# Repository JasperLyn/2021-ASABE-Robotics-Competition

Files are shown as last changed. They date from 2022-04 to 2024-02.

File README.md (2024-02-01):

# Strawberry Nursery Robot - Mr. Y

This is a repository for a project in **2021 ASABE Robotics Competition**, which includes circuit design document, robot control, machine vision and Structure design file. If you are interested in ASABE Robotics Competition, please search more information at official website of [ASABE Robotics Competition](https://asabe.org/Robotics).

## Guide

There are four main parts of the robot.

+ Mechanical Structure (please refer to `Model`)
+ Circuit Design (please refer to `Circuit Design`)
+ Machine Vision (please refer to `src`)
+ Control (please refer to `src`)

## Video Presentation
Team Qizhen Lakers- 2nd Place (Best Electronic Presentation) in the 2021 ASABE Robotics Competition (https://www.youtube.com/watch?v=8VvXFQ61o2o "Team Qizhen Lakers- 2nd Place (Best Electronic Presentation) in the 2021 ASABE Robotics Competition")

## Paper Report

For detailed technical development information, please refer to `Report Document/The Report of Qizhen Lakers`

## Definition of Design Objectives and Criteria

The robot to be designed for this competition should have the ability to recognize the white and yellow leaves of strawberry plants and complete the counting display. In order to achieve the goal perfectly, a detailed and specific division was made to complete the task efficiently and accurately. The sub-points are as follows.

1. Robot needs to have a navigation function without guidelines.
2. Identify white flowers and yellow leaves on each strawberry plant.
3. Transfer detection results of individual plants to a server program for scoring and field map generation.
4. Minimize the weight of the robot and increase the contact area to reduce the pressure.
5. No damage to the plant.
6. No human intervention to the robot.
7. Have a start button that judges can use to initiate a competition trial and an emergency stop button to fully shut down the entire system.

In the design of robot, we are committed to assure better performance, stronger environmental adaptability, and expandability with more development prospects.

## Originality

### Originality

#### Innovative Linkage Design

We use the combination mechanism of slider and linkage to realize the full unfolding of double cameras bracket and create the development condition for double sides detection. And the linkage mechanism has strong scalability, which can reach different unfolding results by adding nodes, connecting rods or linkage structures to meet a variety of needs, and can also add end-effectors at the end of the linkage to achieve more functions.

#### Lower Pressure

We adopt the crawler trolley structure and make the optimal design for the actual production situation of field operation by calculating and selecting the appropriate size of active wheels, tensioning wheels and load-bearing wheels and determining the optimal spacing to share the pressure to the maximum extent and reduce the impact on soil compaction.

#### Infrared-Sensor Tracking

Since we make the robot travel between the board where the strawberry plants were placed and the board as the boundary of the field, we only need to install the infrared sensor at a suitable height (That is, slightly below the thickness of the board on which the strawberry plants are placed), adjust the sensitivity of the signal received by the infrared sensor, and keep the robot moving in a straight line in the desired area by making reasonable use of the differential speed rotation of the stepper motor through the signal measured by the infrared sensor.

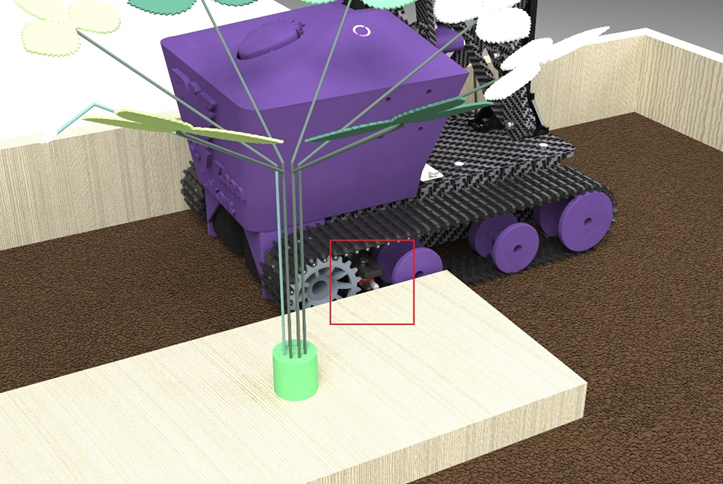
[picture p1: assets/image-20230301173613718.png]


#### Supplemental Light Source

By increasing the fill light band, we make the recognition conditions within the controllable range, eliminate the influence caused by different environmental backgrounds, increase the contrast between the recognition target and the background, and make the robot have better self-adaptability.

#### Multi-threaded Process

We use Raspberry Pi as both processor and control component, and all electronic devices of the robot are controlled through the Raspberry Pi. Calling Python's multi-process module, 3 processes of Raspberry Pi run simultaneously, thus giving higher performance and increasing working speed. The tasks of motor and servo rotation, simultaneous image processing recognition of cameras on both sides and wireless transmission are realized.

#### Remote Emergency Brake

Through the wireless transmission module and Bluetooth module of Raspberry Pi, we designed several remote emergency braking solutions. Although there are already both start switch and emergency brake switch on the robot, considering that there are certain safety hazards of actually approaching the brake when an unpredictable emergency occurs, we made a remote emergency brake switch, which is connected to the Bluetooth module, thus controlling the operation of the Raspberry Pi. In addition, using WIFI wireless communication technology, we can access the graphical interface of the Raspberry Pi for operation. Since all the robot components are controlled by the Raspberry Pi, we can stop the operation of the Raspberry Pi at any moment and thus stop the robot operation. Of course, this does not allow the robot to cut off the power supply system, so we designed an emergency brake switch on the robot to directly cut off the power supply.

## Hardware Description of the Mechanical Structure

### Crawler Structure

In order to reduce the impact on soil compaction and to allow the robot to adapt to a wider range of road environments, we designed a tracked travel mechanism.

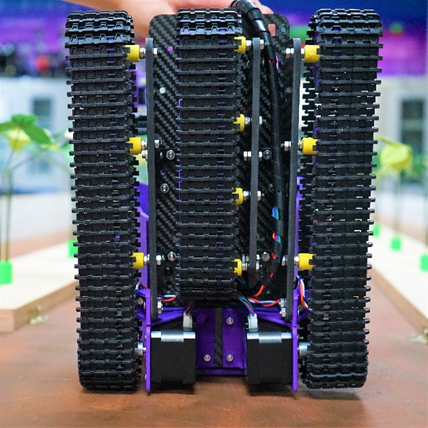
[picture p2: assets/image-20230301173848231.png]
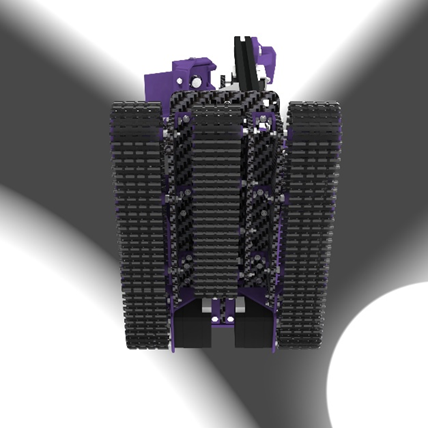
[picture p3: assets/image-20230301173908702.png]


The outer two tracks are long tracks with a ground length of 223.5 mm and a width of 45 mm, equipped with one active wheel, one tensioning wheel and two load-bearing wheels. The middle track is a short track with a ground length of 160 mm and a width of 45 mm, and is equipped with four load-bearing wheels. By reviewing the relevant literature, we calculated the radius and spacing of the active wheel, tensioner wheel and load-bearing wheel. Under the size limitation, we selected the optimal size and spacing.

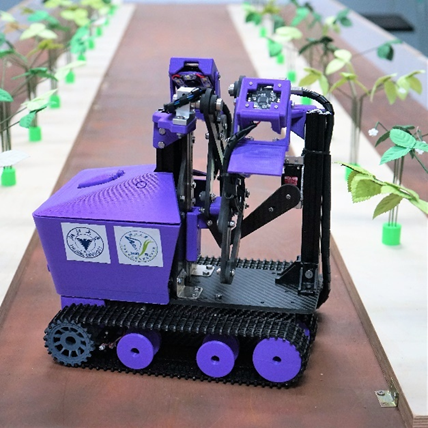
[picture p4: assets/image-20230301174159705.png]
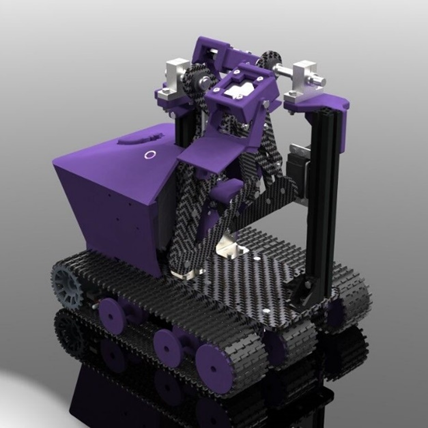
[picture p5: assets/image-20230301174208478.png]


| **Type  of wheel**  | **Radius** |
| :---: | :---: |
| Active  wheel | 25.65  mm  |
|  Tensioning  wheel  | 26.65  mm  |
| Load-bearing  wheel | 20.00  mm  |

### Expanded Mechanical Structure

To simplify the actuator, we use a slide rail and a single-degree-of-freedom extension mechanism with multiple links to extend the camera for detection. The multi-stage linkage is articulated by screws and lock nuts, connected to the slide rail by slider connectors, and uses bearings at some of the connections to reduce frictional resistance, and rotates, lifts, and extends under the drive of the servo. As shown in Figure 5-5 and Figure 5-6, with the rational design of 4 connecting rods on each side (8 in total on both sides), we achieved to expand the robot from the initial size of 300 mm × 209.2 mm × 292.5 mm to 300 mm × 440 mm × 528 mm.

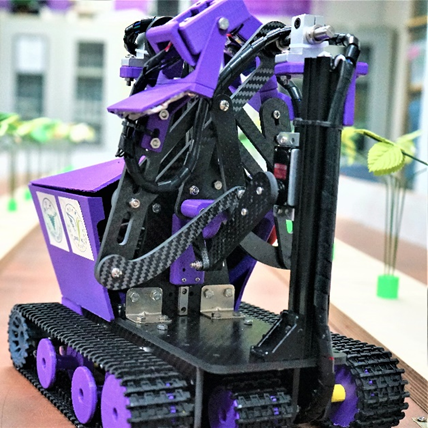
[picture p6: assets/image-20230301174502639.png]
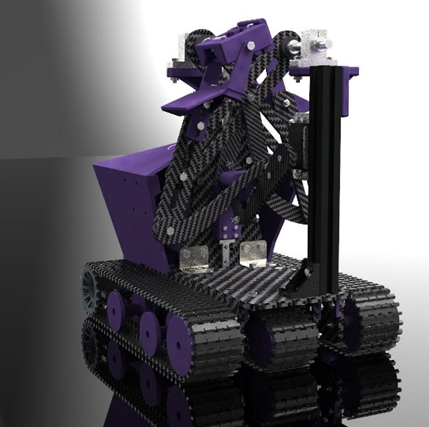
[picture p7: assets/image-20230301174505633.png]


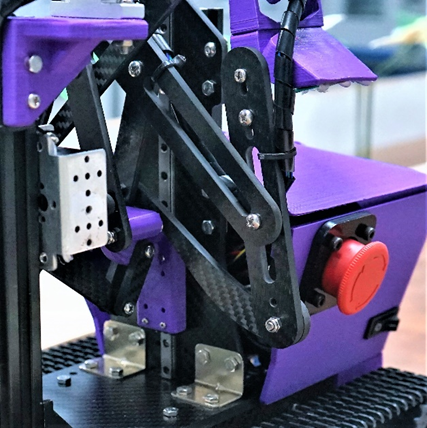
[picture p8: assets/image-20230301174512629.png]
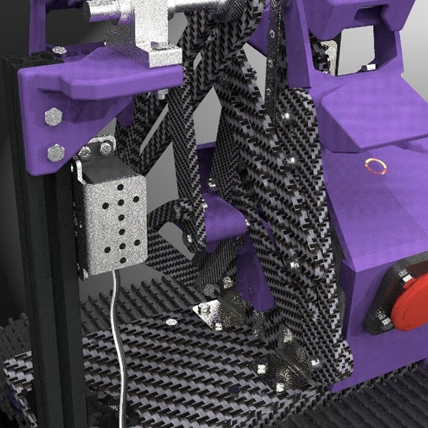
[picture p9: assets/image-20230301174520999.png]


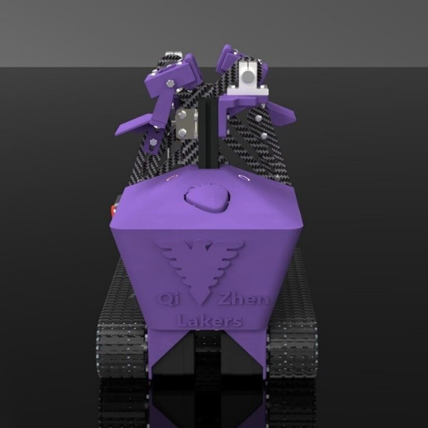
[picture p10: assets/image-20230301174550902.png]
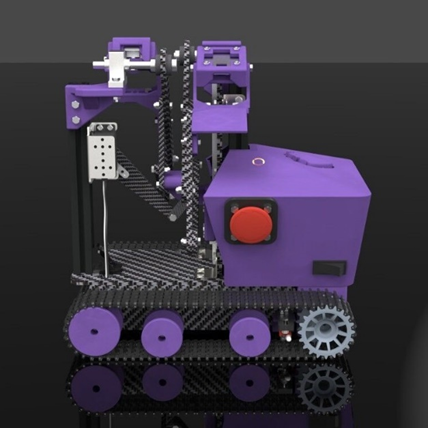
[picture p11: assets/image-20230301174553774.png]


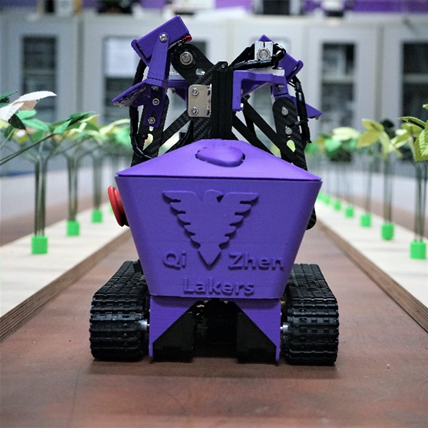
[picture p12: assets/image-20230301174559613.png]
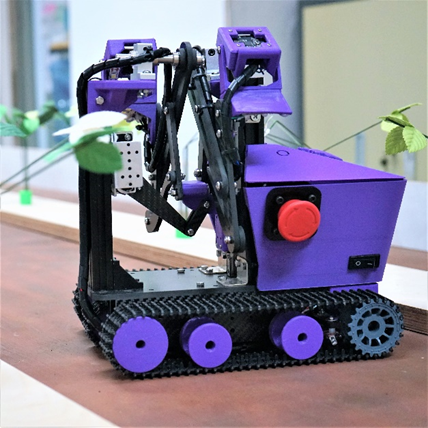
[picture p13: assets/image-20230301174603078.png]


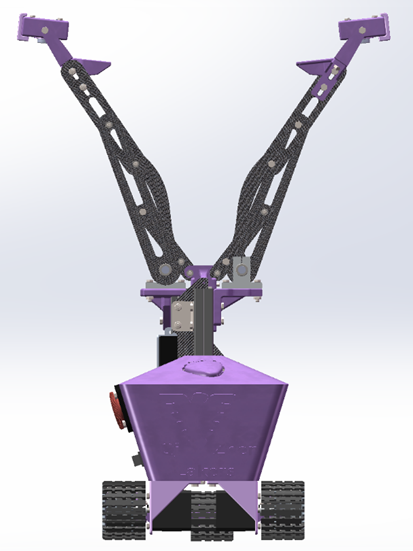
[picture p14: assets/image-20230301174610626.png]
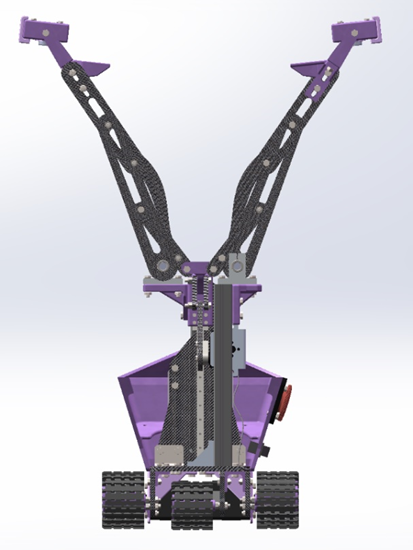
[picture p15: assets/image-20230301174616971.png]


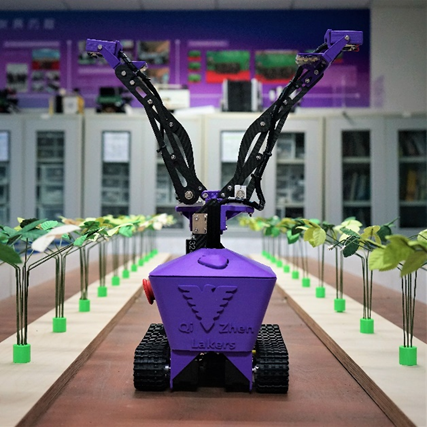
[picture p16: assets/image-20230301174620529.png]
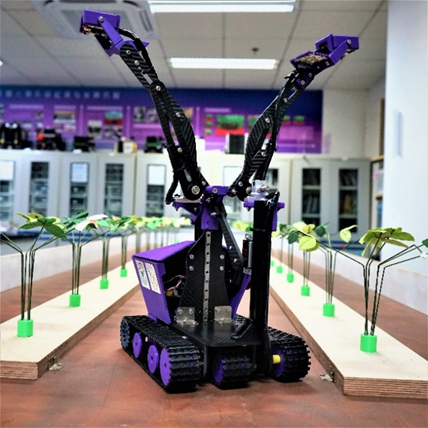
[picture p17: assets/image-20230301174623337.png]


### Adjustable Field of View

In order to facilitate the adjustment of the camera view, we designed a camera connector adjustable in angle.

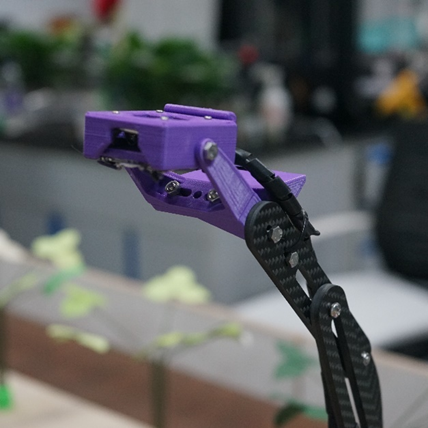
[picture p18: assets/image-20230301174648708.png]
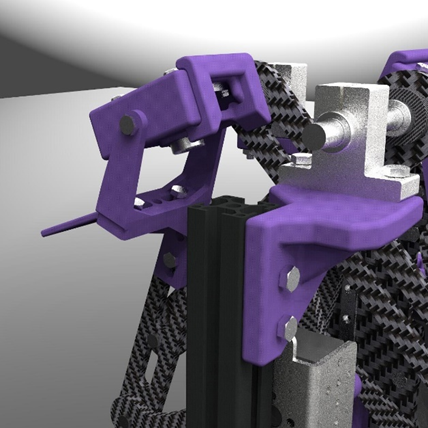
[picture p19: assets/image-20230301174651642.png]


### Tracking Design and Walking Route Map

As shown in Figure 7-2, the robot sends and receives the infrared signal reflected back from the wooden board through two infrared sensors installed between the active and load-bearing wheels on the outer track to determine the position of the site it is in, and adjusts its direction by controlling the differential rotation of stepper motors through Raspberry Pi to ensure that the robot can achieve a straight line in the site along the path as shown in Figure 7-3 to provide the best position for detection.

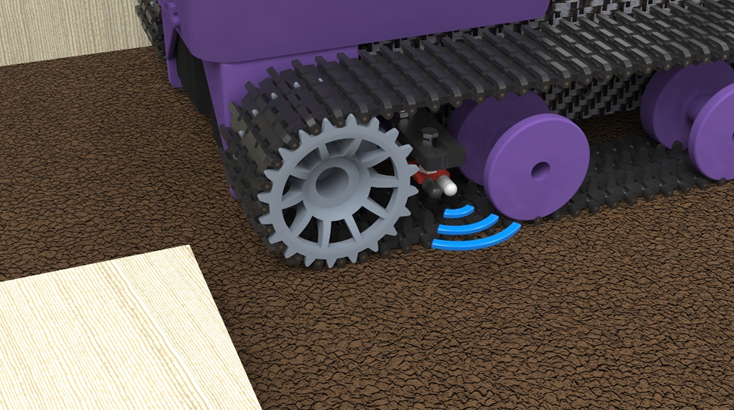
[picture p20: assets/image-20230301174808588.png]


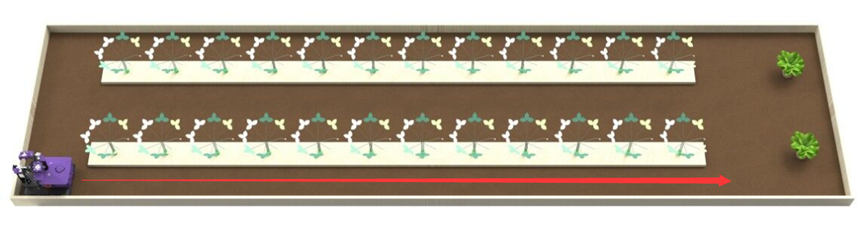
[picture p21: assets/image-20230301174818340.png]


## Machine Vision

### Holder detection

After the robot starts to run, it first identifies the holder. We use the color and shape characteristics of the holder to match the data obtained from the camera, and when the camera moves to the top of the holder, we save the image acquired by the camera instantly for subsequent processing, and get the coordinate information of the holder center.

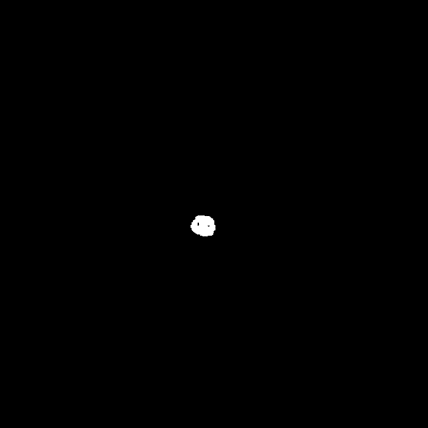
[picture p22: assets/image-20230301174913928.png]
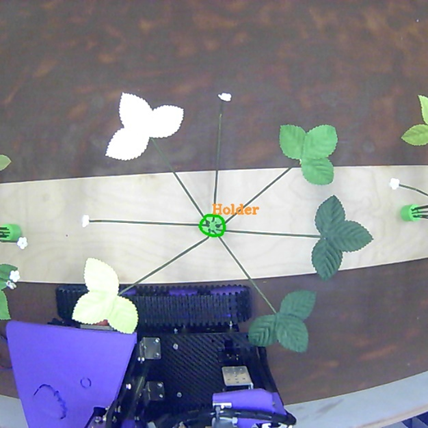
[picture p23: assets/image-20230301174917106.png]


### Leaf detection

After getting the image directly above the plant, the colors in the image are extracted using the green, yellow and white thresholds, respectively. The filtered images of each color channel are filtered to obtain images with smoother borders, and the area and shape parameters of the continuous areas in them are calculated, while the noisy parts with obviously small areas or narrow shapes are filtered. The image of each color channel is processed as mentioned above to get a grayscale image containing only leaves, and the leaves of each color in it are counted in order to store the number of corresponding color leaves.

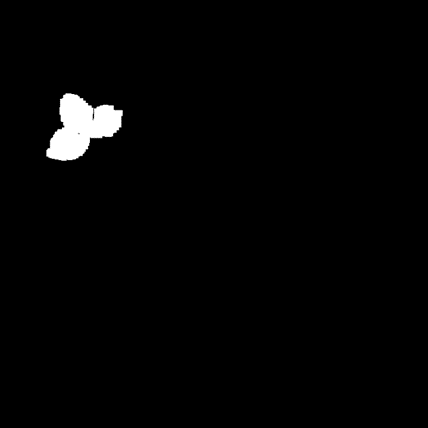
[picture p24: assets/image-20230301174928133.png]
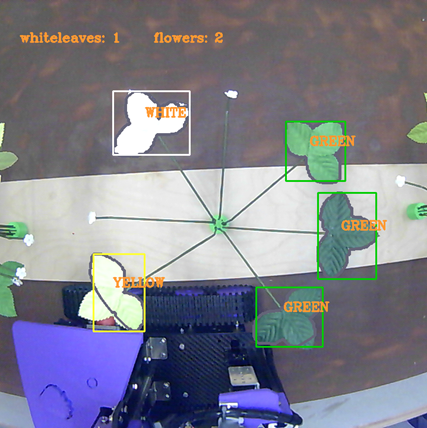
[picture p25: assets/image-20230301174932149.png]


### Flower detection

In particular, the results after the white threshold extraction in the previous session are re-processed with filtering and area calculation, and graphical matching is added to obtain the detection results of white flowers.

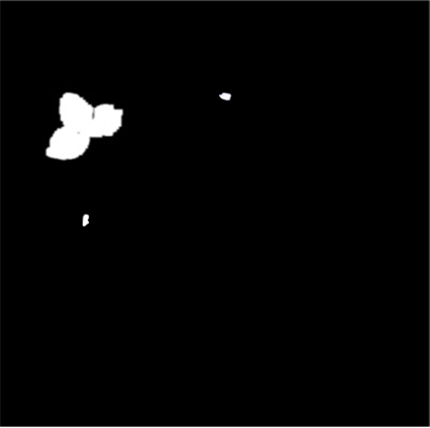
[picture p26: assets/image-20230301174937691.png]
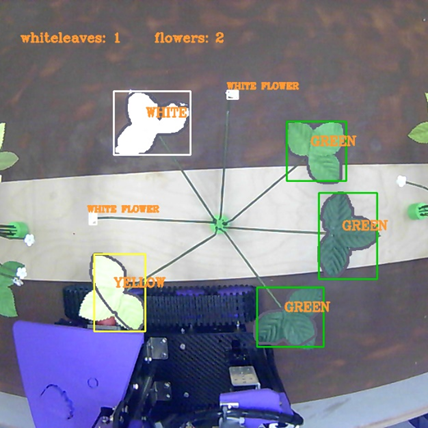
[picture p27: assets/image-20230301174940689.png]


### Stem detection

Similarly, we use the characteristic values of stem color to filter specific locations in the image to obtain a grayscale image of the stems for counting the stems. 

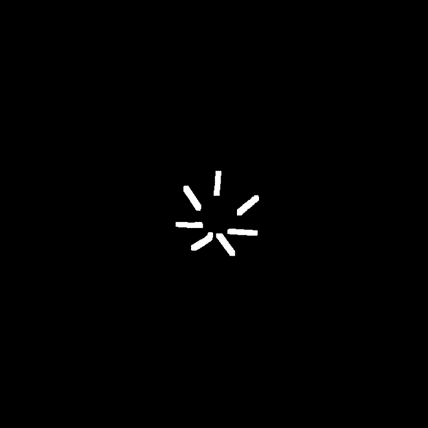
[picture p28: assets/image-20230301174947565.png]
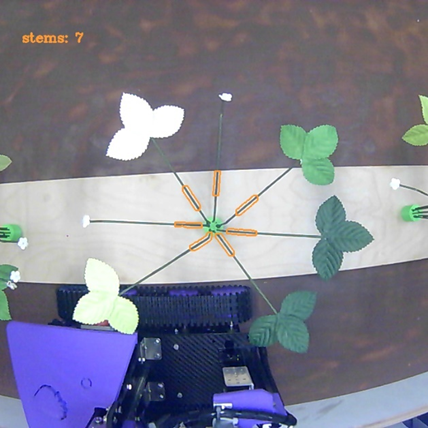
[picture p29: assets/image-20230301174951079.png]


## Logic flowchart of detection

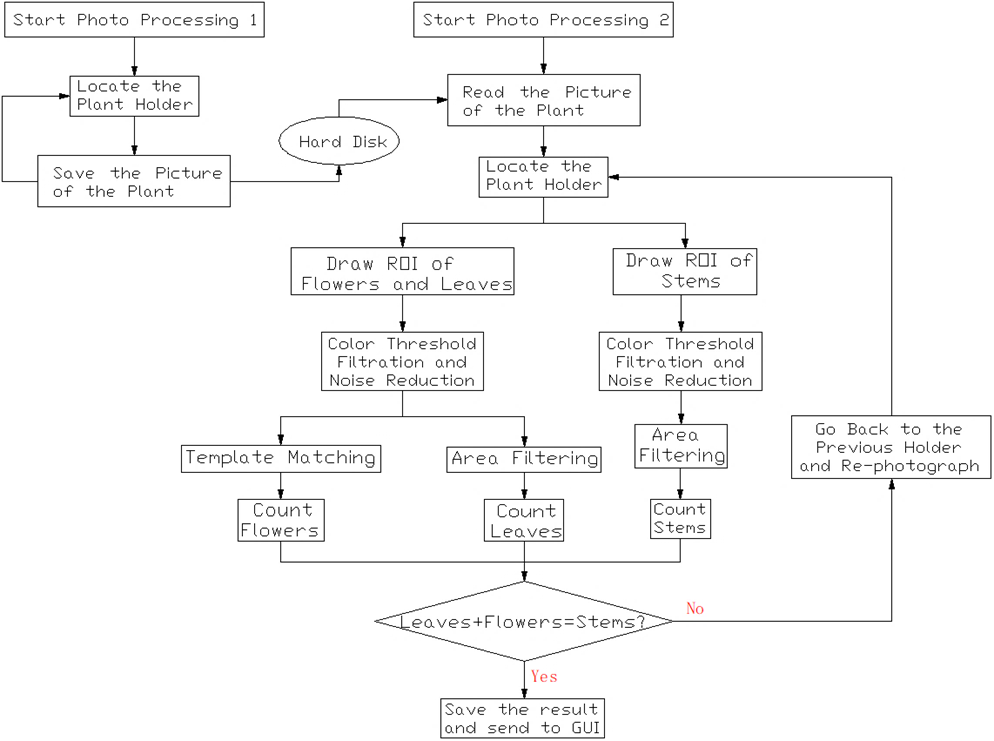
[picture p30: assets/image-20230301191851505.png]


## Logic flowchart of main program

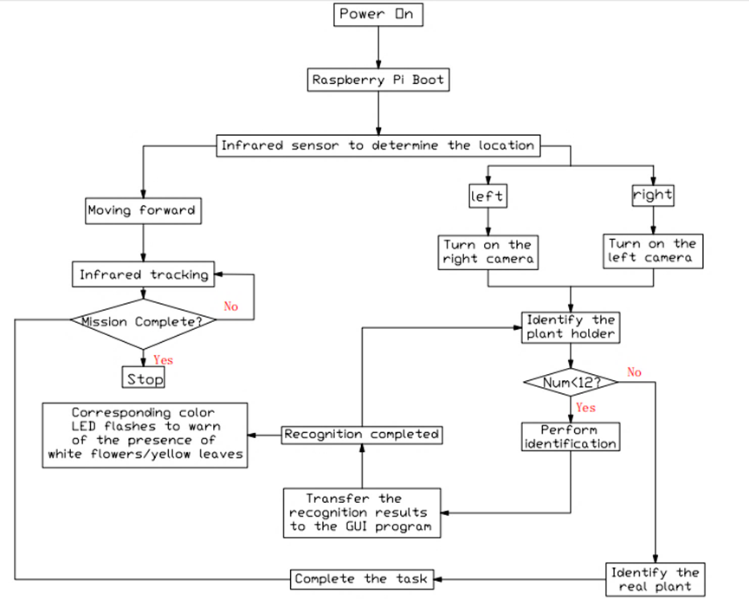
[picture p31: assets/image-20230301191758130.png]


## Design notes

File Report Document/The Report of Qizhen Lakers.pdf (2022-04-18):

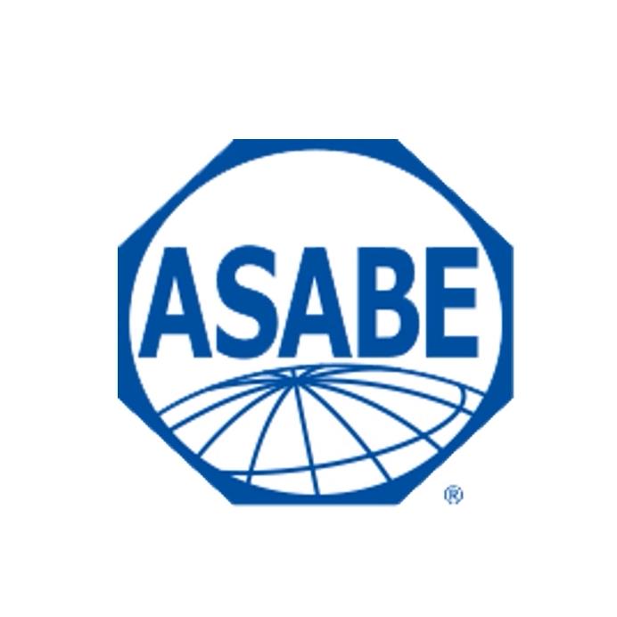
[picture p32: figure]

# 2020 ASABE Student Robotics Challenge

# Robot Design Report

Division | : | Standard
Team Name : | Qizhen Lakers
Advisors | : | Zunzhong Ye, Yonghua Yu,
| | Huanyu Jiang
University | : | Zhejiang University
Captain | : | Yiyuan Lin
Email | : | 3190102104@zju.edu.cn
members | : | Yuliang Zhou, Daoyuan Jin,
| | Xinyue Sun, Yilin Zhang
Date | : | 06/30/2021

## Catalog

Qizhen Lakers 2021 ASABE Student Robotics Competition

## 1 Team Members

In order to complete the 2021 ASABE student robotics challenge, we formed a five-member

team of all sophomore undergraduates, and the specialty of the team members and the tasks we were

responsible for in the challenge are shown in Table 1-1.

Table 1-1 Profiles of team members

Name | Specialty | Assigned tasks | Note

Yiyuan Lin

Code writing and debugging

C, Python

PCB design

·Raspberry Pi code writing and

debugging

·Identification

·Robot assembly

·PCB design

·Paper writing

Captain

Undergraduate

Sophomore

Yuliang Zhou

AutoCAD mechanical drawing

SolidWorks 3D modeling

Assembly of robot mechanism

·Mechanical structure design

·AutoCAD 2D drawing

·SolidWorks 3D modeling

·Robot assembly

Member

Undergraduate

Sophomore

Daoyuan Jin

Python

Code writing and debugging

·Identification

·Raspberry Pi + OpenCV code

writing and debugging

·Paper writing

Member

Undergraduate

Sophomore

Xinyue Sun

Hardware welding

Video Production and Editing

·Purchase and reimbursement

·Hardware welding

·Video Production and Editing

Member

Undergraduate

Sophomore

Yilin Zhang

SolidWorks 3D modeling

Assembly of robot mechanism

·SolidWorks 3D modeling

·Robot assembly

·Paper writing

Member

Undergraduate

Sophomore

## 2 Establishment of Need and Benefit to Agriculture

## 2.1 Strawberry Plant Overview

Strawberry is a perennial herb with a plant height of about 30 cm and a shallow root system,

suitable for growth in a loose and fertile soil with good drainage. The leaves are dark green, oval in

shape, and dark green if the plant is regularly fertilized, and it performs physiological functions of

photosynthesis, respiration, and storage.

Strawberries can flower and bear fruit all year round. As shown in Figure 2-1, each strawberry

plant generally has 2-3 inflorescences, each inflorescence bears 3-30 flowers and 10-40 small fruits.

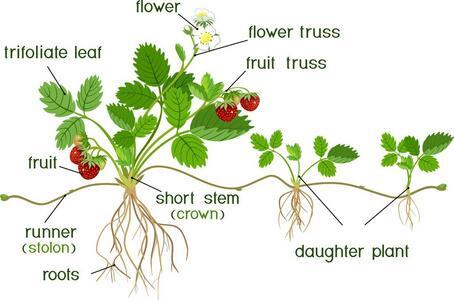
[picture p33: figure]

Figure 2-1 Strawberry

## 2.2 Why to Find Yellow Leaves

As shown in Figure 2-2, due to large changes in ambient temperature or trace element

deficiency, the plant can wither and the leaves turn yellow. The loss of photosynthesis ability of the

yellow leaves will affect the normal growth of the plant, which in turn will lead to yield reduction,

thus causing economic losses, which need to be identified and removed in time.

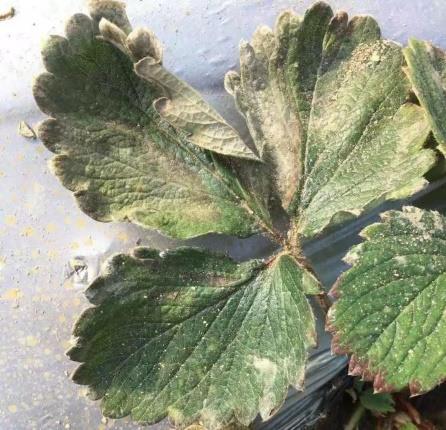
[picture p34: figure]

Figure 2-2 Yellow leaves of strawberry

## 2.3 Why to Remove White Flowers

As shown in Figure 2-3, These small fruits have no harvesting value. Without being removed,

unfair competition for limited nutrients between the fruits that are on the same plant will occur.

Therefore, in strawberry cultivation, flower thinning can reduce the nutrient consumption, so that

the retained flowers are well developed, the fruit is neatly set, and the appearance and quality of the

fruit can be improved accordingly. In order to increase the yield and prevent premature decay, while

making the ripening period concentrated and saving harvesting labor.

Figure 2-3 White flower of strawberry

## 2.4 Design Meaning

① Identify and count the yellow leaves of strawberry plants to reduce the impact of yellow

leaves that have lost their light and ability on the plants, thus promoting the healthy growth of plants. ② Identify the white flowers of strawberry plants and count them for agricultural transplanting,

so as to reduce fruit competition and nutritional loss of the same plant, make the retained flowers

develop well and fruit set neatly, and improve the appearance and quality of the fruit accordingly,

so as to achieve the purpose of increasing yield and preventing premature decay, and at the same

time make the maturity period concentrated and save harvesting labor.
③ Reduce agricultural labor consumption and lower agricultural production costs.

## 3 Definition of Design Objectives and Criteria

The robot to be designed for this competition should have the ability to recognize the white

and yellow leaves of strawberry plants and complete the counting display. In order to achieve the

goal perfectly, a detailed and specific division was made to complete the task efficiently and

accurately. The sub-points are as follows.
① Robot needs to have a navigation function without guidelines.

② Identify white flowers and yellow leaves on each strawberry plant.

③ Transfer detection results of individual plants to a server program for scoring and field map

generation.
④ Minimize the weight of the robot and increase the contact area to reduce the pressure.

⑤ No damage to the plant.

⑥ No human intervention to the robot.

⑦ Have a start button that judges can use to initiate a competition trial and an emergency stop

button to fully shut down the entire system.

In the design of robot, we are committed to assure better performance, stronger environmental

adaptability, and expandability with more development prospects.

## 4 Approach and Originality

## 4.1 Approach

### 4.1.1 Hardware

For farm work machinery, the pressure of the robot on the farm is proportional to the degree of

damage to the farm by the robot. Smaller pressure is conducive to actual production and application.

Therefore, we adopt a crawler structure with stepper motors for driving to obtain the maximum

contact area under the same quality, thereby reducing the pressure of the vehicle on the ground as

much as possible. In order to stretch the robot from a smaller size to a higher height to obtain the

largest possible field of view with higher adjustability, we used a mechanical structure with a rod

group and slide rails, allowing the mechanism to be fully expanded, and a wide-angle camera to

obtain a wider field of view. We use a lithium battery with an output voltage of 16V to power the

Raspberry Pi through the UBEC module, and a voltage regulator module to power and control

various electronic components with different operating voltages.

### 4.1.2 Software

In actual production, most agricultural operation robots can only achieve unilateral operation,

which reduces the operation efficiency and increases the time cost. We planned to use a 4th

generation Raspberry Pi with 2GB RAM as not only the processor but also the main controller. The

Raspberry Pi is connected to all electronic devices on the robot through voltage regulator modules

and USB interfaces. For recognition and control tasks, the Raspberry Pi handles them separately

through its multi-threaded processing capability and our robot has bilateral simultaneous

recognition capability. The Raspberry Pi extends the combined linkage mechanism through the servo and receives the signals returned by the bilateral planks through the infrared sensors for tracing.

Finally, the Raspberry Pi transmits the recognition result to a dedicated server computer through the

wireless transmission module.

## 4.1.3 Conclusion of Approach

Overall, our robot controls all the electronic components on the robot through the Raspberry

Pi. The Raspberry Pi drives stepper motors and servo, processes signals from infrared sensors

through GPIO pins for tracing, connects to camera through USB port to process images captured by

the camera, and uploads recognition results to a dedicated server computer through a wireless

transmission module.

## 4.2 Originality

### 4.2.1 Innovative Linkage Design

We use the combination mechanism of slider and linkage to realize the full unfolding of double

cameras bracket and create the development condition for double sides identification. And the

linkage mechanism has strong scalability, which can reach different unfolding results by adding

nodes, connecting rods or linkage structures to meet a variety of needs, and can also add end-

effectors at the end of the linkage to achieve more functions.

### 4.2.2 Lower Pressure

We adopt the crawler trolley structure and make the optimal design for the actual production

situation of field operation by calculating and selecting the appropriate size of active wheels,

tensioning wheels and load-bearing wheels and determining the optimal spacing to share the

pressure to the maximum extent and reduce the impact on soil compaction.

### 4.2.3 Infrared-Sensor Tracking

Since we make the robot travel between the board where the strawberry plants were placed and

the board as the boundary of the field, we only need to install the infrared sensor at a suitable height

(That is, slightly below the thickness of the board on which the strawberry plants are placed, as

shown in Figure 4-1), adjust the sensitivity of the signal received by the infrared sensor, and keep

the robot moving in a straight line in the desired area by making reasonable use of the differential

speed rotation of the stepper motor through the signal measured by the infrared sensor.

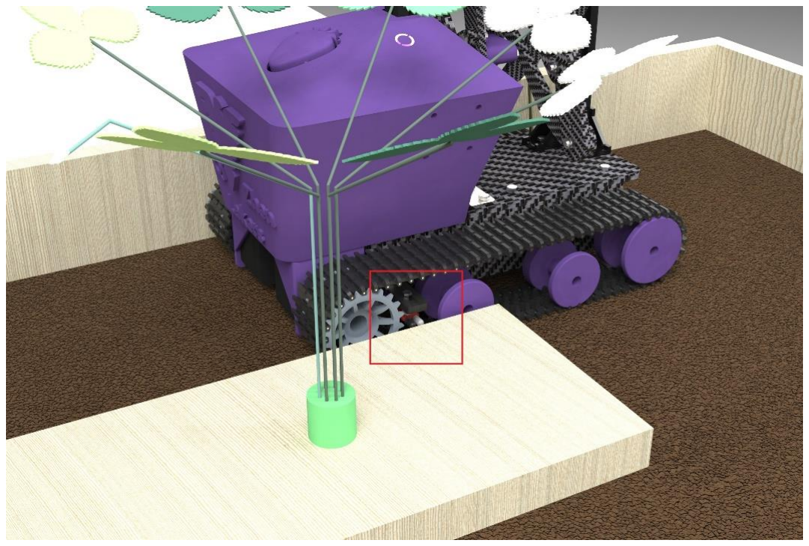
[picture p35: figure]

Figure 4-1 Installation height of the infrared sensor

### 4.2.4 Supplemental Light Source

By increasing the fill light band, we make the recognition conditions within the controllable

range, eliminate the influence caused by different environmental backgrounds, increase the contrast

between the recognition target and the background, and make the robot have better self-adaptability.

### 4.2.5 Multi-threaded Process

We use Raspberry Pi as both processor and control component, and all electronic devices of

the robot are controlled through the Raspberry Pi. Calling Python's multi-process module, 3

processes of Raspberry Pi run simultaneously, thus giving higher performance and increasing

working speed. The tasks of motor and servo rotation, simultaneous image processing recognition

of cameras on both sides and wireless transmission are realized.

### 4.2.6 Remote Emergency Brake

Through the wireless transmission module and Bluetooth module of Raspberry Pi, we designed

several remote emergency braking solutions. Although there are already both start switch and

emergency brake switch on the robot, considering that there are certain safety hazards of actually

approaching the brake when an unpredictable emergency occurs, we made a remote emergency

brake switch, which is connected to the Bluetooth module, thus controlling the operation of the

Raspberry Pi. In addition, using WIFI wireless communication technology, we can access the

graphical interface of the Raspberry Pi for operation. Since all the robot components are controlled

by the Raspberry Pi, we can stop the operation of the Raspberry Pi at any moment and thus stop the robot operation. Of course, this does not allow the robot to cut off the power supply system, so we

designed an emergency brake switch on the robot to directly cut off the power supply.

## 5 Hardware Description of the Mechanical Structure

## 5.1 Crawler Structure

In order to reduce the impact on soil compaction and to allow the robot to adapt to a wider

range of road environments, we designed a tracked travel mechanism, as shown in Figure 5-1.

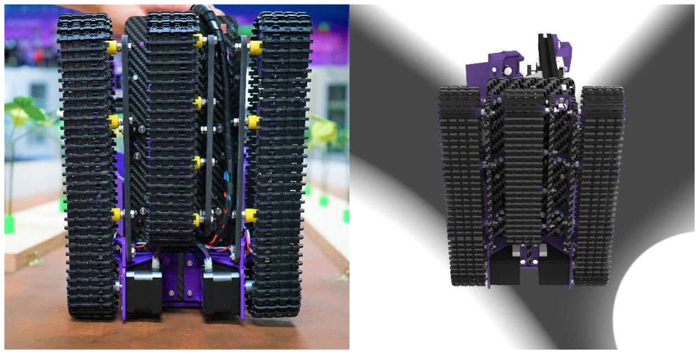
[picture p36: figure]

(a) Physical picture | (b) Model picture in SolidWorks

Figure 5-1 Crawler chassis

The outer two tracks are long tracks with a ground length of 223.5 mm and a width of 45 mm,

equipped with one active wheel, one tensioning wheel and two load-bearing wheels. The middle

track is a short track with a ground length of 160 mm and a width of 45 mm, and is equipped with

four load-bearing wheels. By reviewing the relevant literature, we calculated the radius and spacing

of the active wheel, tensioner wheel and load-bearing wheel. Under the size limitation, we selected

the optimal size and spacing, as shown in Figure 5-2 and Table 5-1.

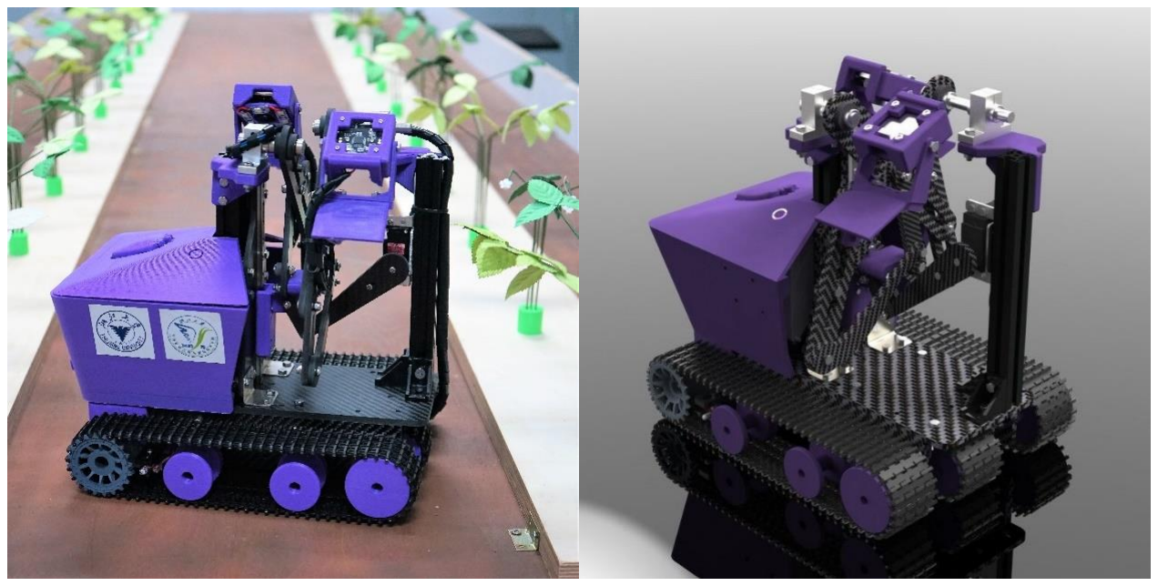
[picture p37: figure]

(a) Photo of the robot | (b) Robot model in SolidWorks

Figure 5-2 Photo of the robot(a) and the robot model in SolidWorks(b)

Table 5-1 Radius of the three types of wheels

Type of wheel | Radius
Active wheel | 25.65 mm
Tensioning wheel | 26.65 mm
Load-bearing wheel | 20.00 mm

## 5.2 Expanded Mechanical Structure

To simplify the actuator, we use a slide rail and a single-degree-of-freedom extension

mechanism with multiple links to extend the camera for identification. The multi-stage linkage is

articulated by screws and lock nuts (as shown in Figure 5-3), connected to the slide rail by slider

connectors (as shown in Figure 5-4), and uses bearings at some of the connections to reduce

frictional resistance, and rotates, lifts, and extends under the drive of the servo. As shown in Figure

5-5 and Figure 5-6, with the rational design of 4 connecting rods on each side (8 in total on both

sides), we achieved to expand the robot from the initial size of 300 mm × 209.2 mm × 292.5 mm to

300 mm × 440 mm × 528 mm.

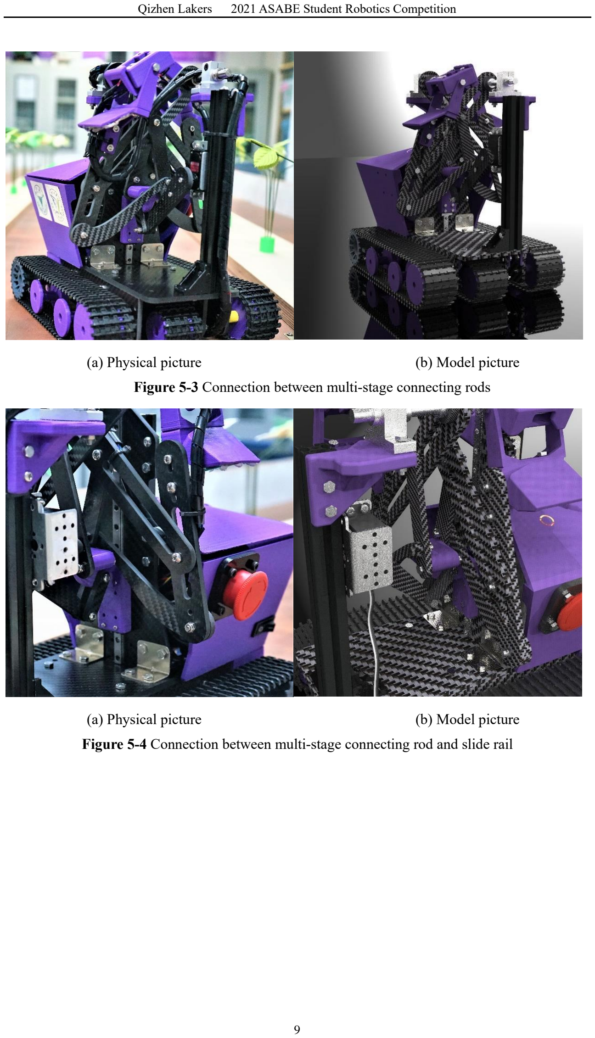
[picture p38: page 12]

(a) Physical picture | (b) Model picture

Figure 5-3 Connection between multi-stage connecting rods

(a) Physical picture | (b) Model picture

Figure 5-4 Connection between multi-stage connecting rod and slide rail

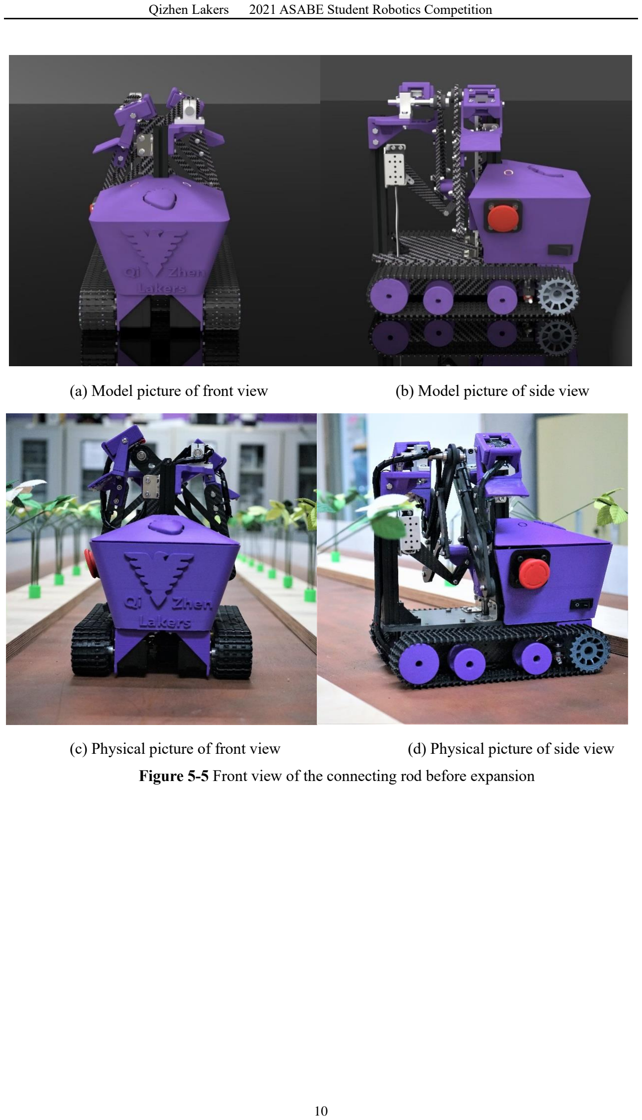
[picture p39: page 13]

(a) Model picture of front view | (b) Model picture of side view
(c) Physical picture of front view | (d) Physical picture of side view

Figure 5-5 Front view of the connecting rod before expansion

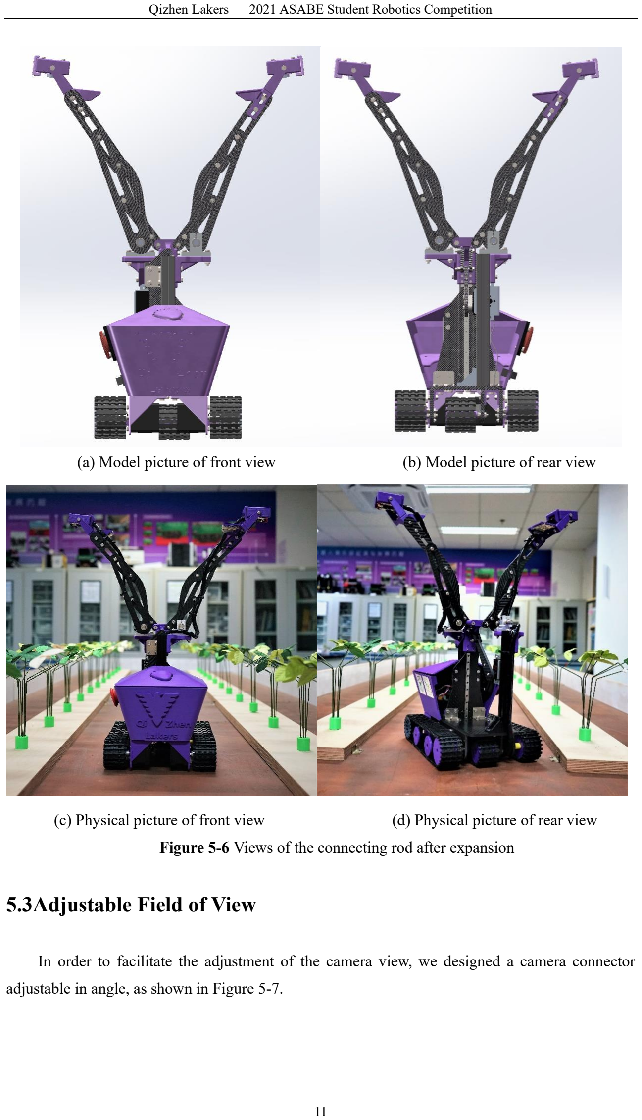
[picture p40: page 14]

(a) Model picture of front view | (b) Model picture of rear view
(c) Physical picture of front view | (d) Physical picture of rear view

Figure 5-6 Views of the connecting rod after expansion

## 5.3Adjustable Field of View

In order to facilitate the adjustment of the camera view, we designed a camera connector

adjustable in angle, as shown in Figure 5-7.

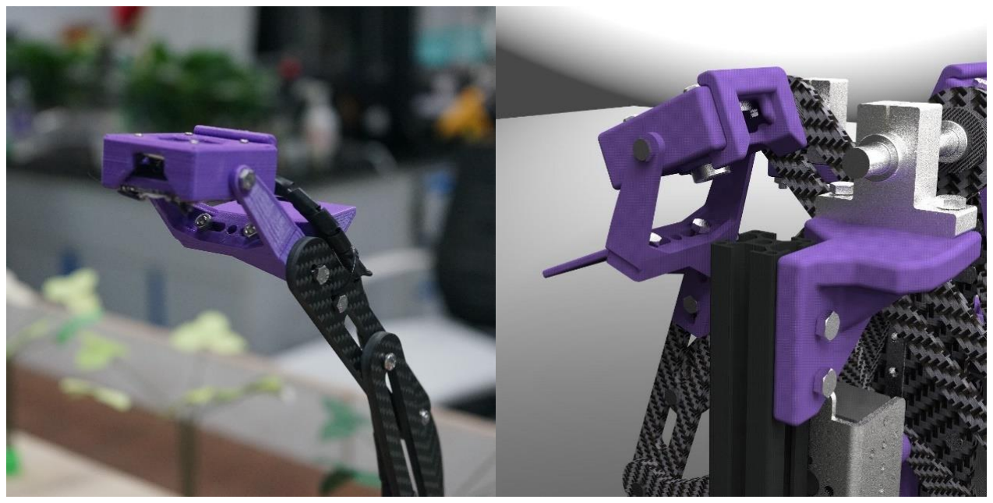
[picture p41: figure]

(a) Physical picture | (b) Model picture

Figure 5-7 Camera connector

## 6 Hardware Description of the Main Electronic Component

## 6.1 Raspberry Pi

We chose Raspberry Pi 4B as the processor to control the whole robot work. It is an ARM

based satellite computer motherboard with SD/MicroSD card as memory drive, USB and Ethernet

ports around the card motherboard, TV output port for video analog signal and HDMI HD video

output port. With a 64-bit quad-core processor running at 1.5Ghz, dual displays supporting up to 4K

resolution refreshed at 60fps, and up to 4GB RAM, performance is significantly improved in terms

of processor speed, multimedia and memory with desktop performance comparable to entry-level

x86 PC systems.

## 6.2 Stepper Motor

The crawler is driven by Tokugawa's 42HB40-401A stepper motor. This motor works under

the drive circuit, has low heat generation and high efficiency, and can adjust the current level

according to the actual situation, so that it can emit more energy in a compact space.

The 42HB40-401A stepper motor is a two-phase four-wire system with a torque of 0.31 N·m,

rated current of 1.2 A, phase resistance of 3.3 Ω, phase inductance of 5.4 mH, and a mass of 0.22

Kg with a body thickness of 33.5mm.

## 6.3 Servo

We chose MG996 32 Kg black digital servo. This digital servo has fast response, precise angle,

gears of aluminum oxide, double ball bearings with no-load speed of 0.18 s/60° and blocking torque

of 30.8 Kg/cm under operating voltage of 6 V, which is enough to drive the servo to extend the

identification mechanism.

In addition, due to the small internal resistance of this servo, no jitter rudder and blocking

rotation protection function, it can completely get rid of the phenomenon of jitter rudder and

blocking rotation burnout of the servo in operation.

## 6.4 Camera

We chose a commercial camera(720P-1280×720-mjpg/30fps) for image processing of the

target plant. By acquiring the plant image through the camera and using the powerful computing

power of Raspberry Pi to implement more advanced algorithms, we can identify the target more

accurately.

## 6.5 Infrared Sensor

Infrared transmitter tube constantly emits infrared, when the emitted infrared is not reflected

back or is reflected back but the intensity is not large enough, the infrared receiver tube has been in

the off state, at this time the TTL output of the module is high, the corresponding indication diode

has been in the off state; when the detected object appears in the detection range, the infrared is

reflected back and the intensity is large enough, the infrared receiver tube conducts, at this time The

TTL output of the module is low and the indicator diode is lit for testing. The TTL output of the

module is low and the diode is lit for testing.

## 6.6 Circuit Board

We designed custom PCB board for connecting the Raspberry Pi and other electronic

components, the connection between the Raspberry Pi and electronic components is shown in Figure

6-1. (In order to show the connection between electronic components visually and clearly, only an

abbreviated connection diagram is made here, not the actual connection situation)

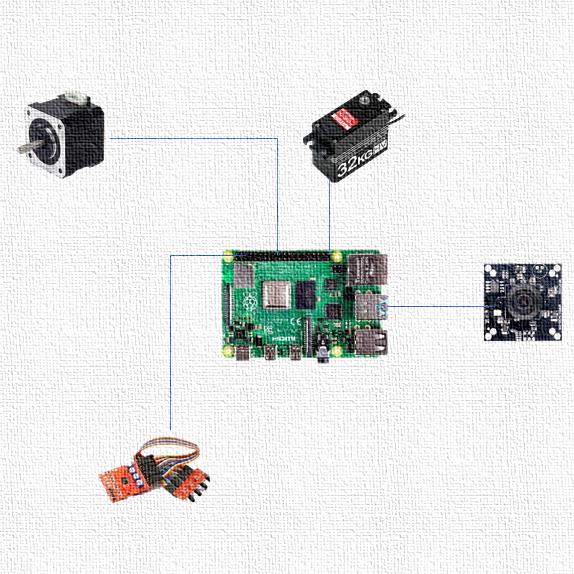
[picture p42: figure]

Figure 6-1 Schematic diagram of the hardware connection

The electronic component we used is shown in Table 6-1

Table 6-1 Main electronic components list

The name of the hardware | Type | Appearance | Amount

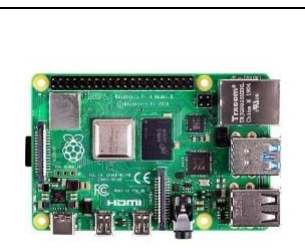
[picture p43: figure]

Raspberry Pi | Raspberry Pi 4B | 1
Stepper motor | 42HB34-401A | 2
Servo | MG996 | 1

Camera

720P-1280×720-

mjpg/30 fps

2

Infrared sensor | HW-096-A | 2

Circuit board

Designed by

ourselves

1

## 7 Software Overview and Logic Flowchart

## 7.1 Main Program Design

The logic of the main program for robot operation is shown in Figure 7-1.

When the power is turned on, Raspberry Pi starts the corresponding multi-threaded program to

determine the location of the site through the infrared sensor and calls the corresponding camera for

the identification task, while the robot tracks through the infrared sensor. When the Raspberry Pi

controls the camera to identify the plant base, it identifies the strawberry plants belonging to the

base and flashes the LEDs of corresponding color to warn the presence of yellow leaves or white

flowers. After each plant is identified, the information about leaves and flowers of the plant is

immediately transferred to the GUI program. For plants that are not identified, we default them as

healthy plants and record the number of yellow leaves and white flowers as 0 temporarily, and

overwrite the result if yellow leaves and white flowers are identified later. After identifying all

twelve plants, the real strawberry plant located at the end of the field is identified, and all tasks are

completed and the robot stops running after the identification is finished.

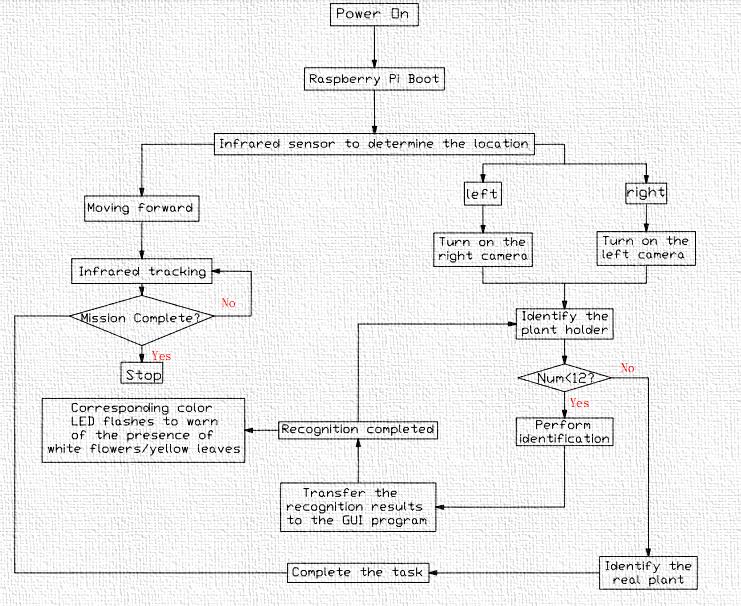
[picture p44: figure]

figure 7-1 Logic flowchart of main program

## 7.2 Tracking Design and Walking Route Map

As shown in Figure 7-2, the robot sends and receives the infrared signal reflected back from

the wooden board through two infrared sensors installed between the active and load-bearing wheels

on the outer track to determine the position of the site it is in, and adjusts its direction by controlling

the differential rotation of stepper motors through Raspberry Pi to ensure that the robot can achieve a straight line in the site along the path as shown in Figure 7-3 to provide the best position for

identification.

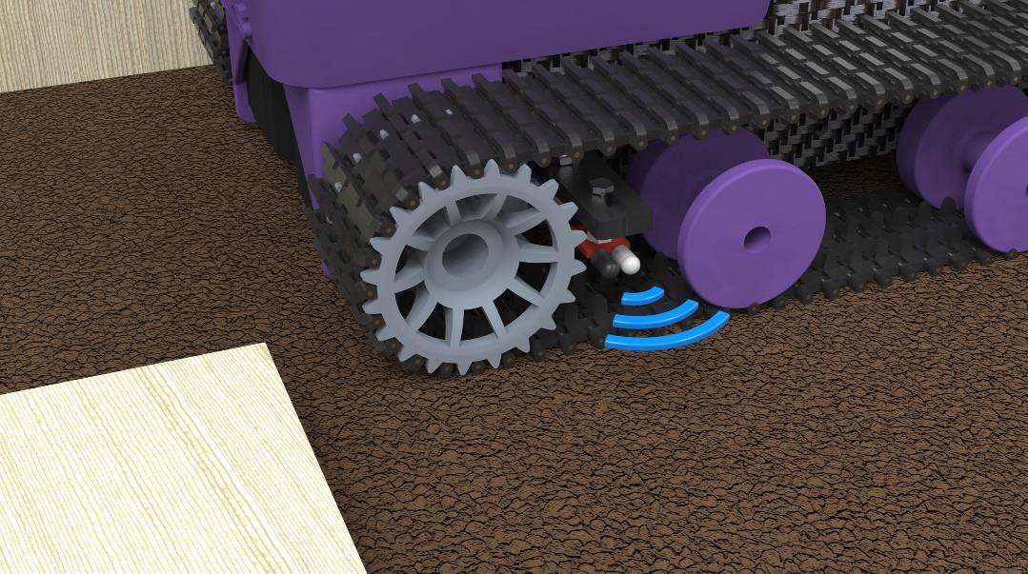
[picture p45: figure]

Figure 7-2 Working principle of infrared sensor

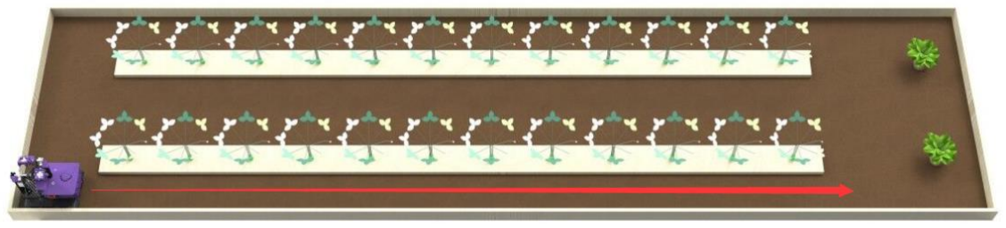
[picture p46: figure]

Figure 7-3 The route of the robot

## 7.3 Machine Vision

### 7.3.1 Holder Identification

After the robot starts to run, it first identifies the holder. We use the color and shape

characteristics of the holder to match the data obtained from the camera, and when the camera moves

to the top of the holder, we save the image acquired by the camera instantly for subsequent

processing, and get the coordinate information of the holder center.

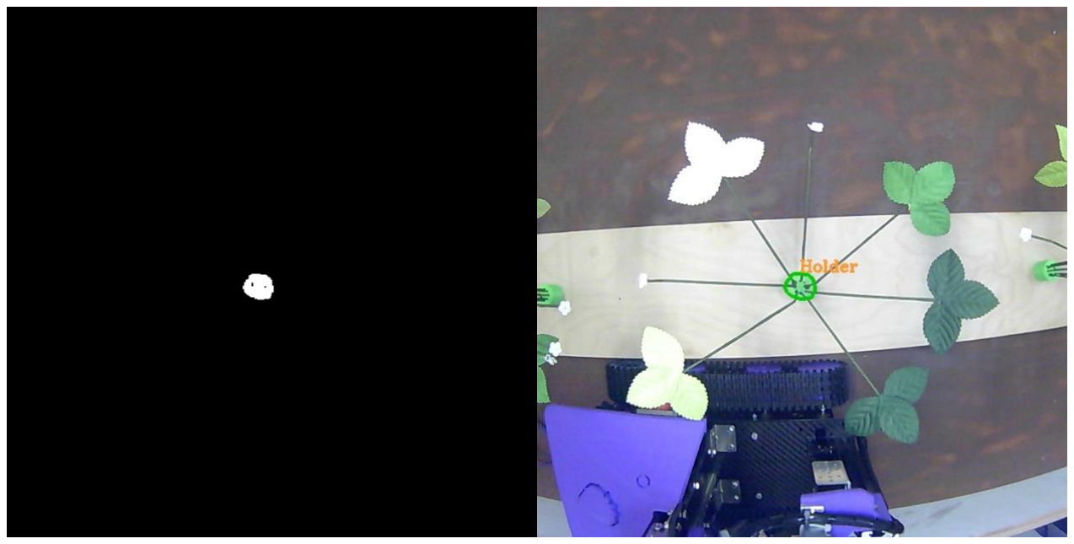
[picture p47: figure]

Figure 7-4 Binarization of holder identification

### 7.3.2 Leaf Identification

After getting the image directly above the plant, the colors in the image are extracted using the

green, yellow and white thresholds, respectively. The filtered images of each color channel are

filtered to obtain images with smoother borders, and the area and shape parameters of the continuous

areas in them are calculated, while the noisy parts with obviously small areas or narrow shapes are

filtered. The image of each color channel is processed as mentioned above to get a grayscale image

containing only leaves, and the leaves of each color in it are counted in order to store the number of

corresponding color leaves.

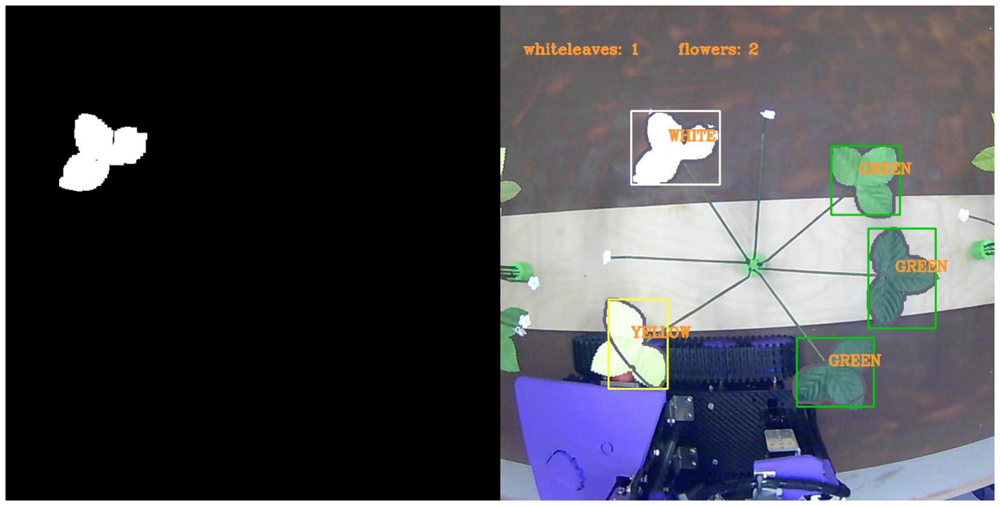
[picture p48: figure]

Figure 7-5 Binarization of leaf identification

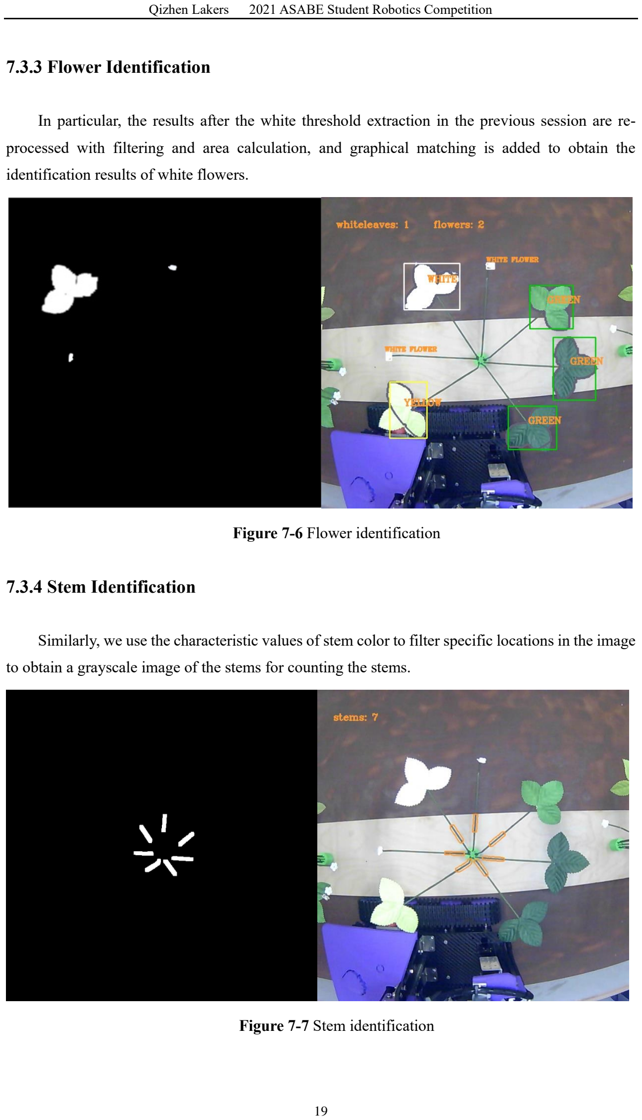
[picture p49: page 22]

### 7.3.3 Flower Identification

In particular, the results after the white threshold extraction in the previous session are re-

processed with filtering and area calculation, and graphical matching is added to obtain the

identification results of white flowers.

Figure 7-6 Flower identification

### 7.3.4 Stem Identification

Similarly, we use the characteristic values of stem color to filter specific locations in the image

to obtain a grayscale image of the stems for counting the stems.

Figure 7-7 Stem identification

### 7.3.5 Auxiliary Methods for Identification

① LED supplementary lighting

We installed LEDs to uniformly illuminate the strawberry plant at the position near the camera

to eliminate the effect on identification and increase the contrast between the strawberry leaves,

white flowers and the background wood panel from ambient light difference to improve the

identification accuracy.
② Region of interests

After getting the result of holder detection, we take the holder as the center of circle and

combine the dimensions of strawberry plant and base to get the radius, and build multiple ROIs for

the locations where stems, flowers and leaves may appear in the camera field of view to narrow

down the identification range. The introduction of ROIs reduces the influence of irrelevant contents

on the identification and help speed up the program operation.
③ Stems Identification

In fact, the results of the analysis of flowers and leaves identification were enough to complete

the task of the competition. Therefore, we use the obtained stems data to check the results of flowers

and leaves identification. If the two results do not match, a new identification is required.

### 7.3.6 Appropriateness of Tests and Performance Data

Considering that in actual agricultural production strawberries are mostly grown in

greenhouses, and the farmer will use different fill light measures according to the actual situation in

order to improve the yield, we adjusted our recognition program to the extent where it can adapt to

a variety of common greenhouse fill light ambient light sources. As shown in Figures 7-8, we

simulated four different ambient light sources: red light, blue-violet light, red light + blue-violet

light, and white fluorescent light. Under the condition that the robot itself is equipped with white

LED light sources for supplemental lighting, we adjusted the appropriate parameters and collected

sufficient data sets for template matching of white flowers. Finally, the accuracy of recognition

results in the three environments is shown in Table 7-1.

Also, demonstrated in Figures 7-8, the impact of the ambient light source on the leaves and

flowers is effectively reduced due to the supplemental lighting measures taken by the robot itself

when identifying the strawberry plants.

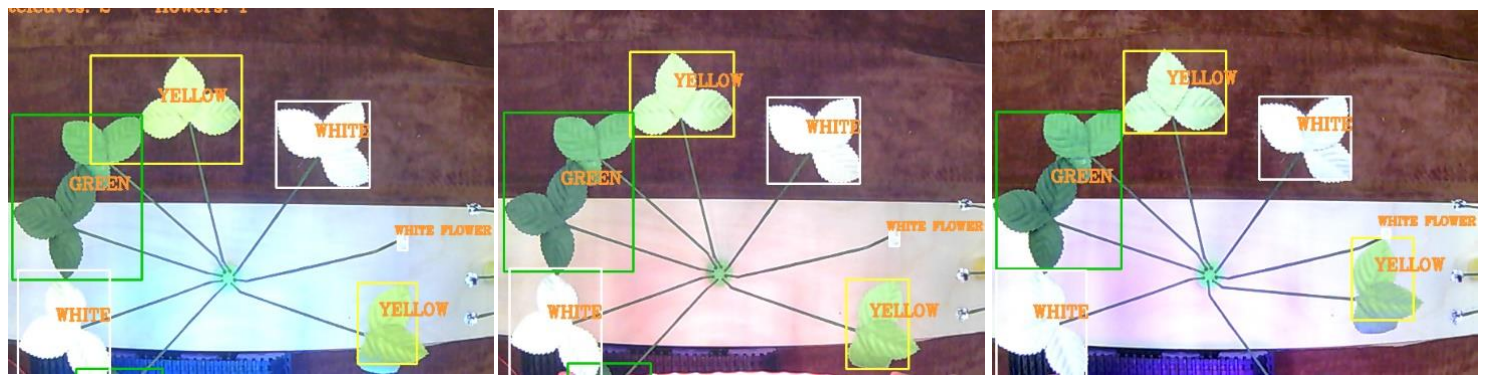
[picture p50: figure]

Figure 7-8 Recognition results under different ambient light sources

Table 7-1 Recognition accuracy under different ambient light sources

Environmental light

sources

Recognition

accuracy

Number of

tests

Overall recognition

accuracy

White fluorescent lamp | 98.5% | >200

89.8%

Red light | 87.5% | 100
Blue violet light | 88.1% | 100
Red light & blue violet light | 76.4% | 100

It should be noted that the accuracy of recognition results here is calculated as the ratio of the

total number of correctly recognized white flowers and yellow leaves to the total number of all white

flowers and yellow leaves. In addition, considering that the robot was designed with the primary

goal of completing the competition, we assigned a higher weight to the white fluorescent

environment, and the parameters of the recognition program were eventually adjusted to the optimal

parameters based on the weights, resulting in the highest total recognition accuracy.

In order to improve the overall speed and fluency of the robot, we used multi-threaded

processing for recognition. Thread 1 is used to identify the plant base to determine the plant location

and take pictures to save them in the memory of the Raspberry Pi. Thread 2 is used to process the

images taken in process 1 (Thread 3 is used to control the robot's advancement and expansion). This

design makes our robot run much faster and smoother, with thread 1 achieving a frame rate of 30

frames per second on the Raspberry Pi 4B and thread 2 processing images at 0.25 ms per image.

The robot does not need to stop while moving forward, which reduces the occurrence of linkage

wobble and greatly improves the overall speed and fluency.

### 7.3.7 Logic Flowchart of Identification

In summary, the Logic Flowchart of our machine vision processing plant information is shown

in Figure 7-9.

Testing under blue-violet light conditions | Testing under red light conditions | Testing under blue-violet & red light conditions

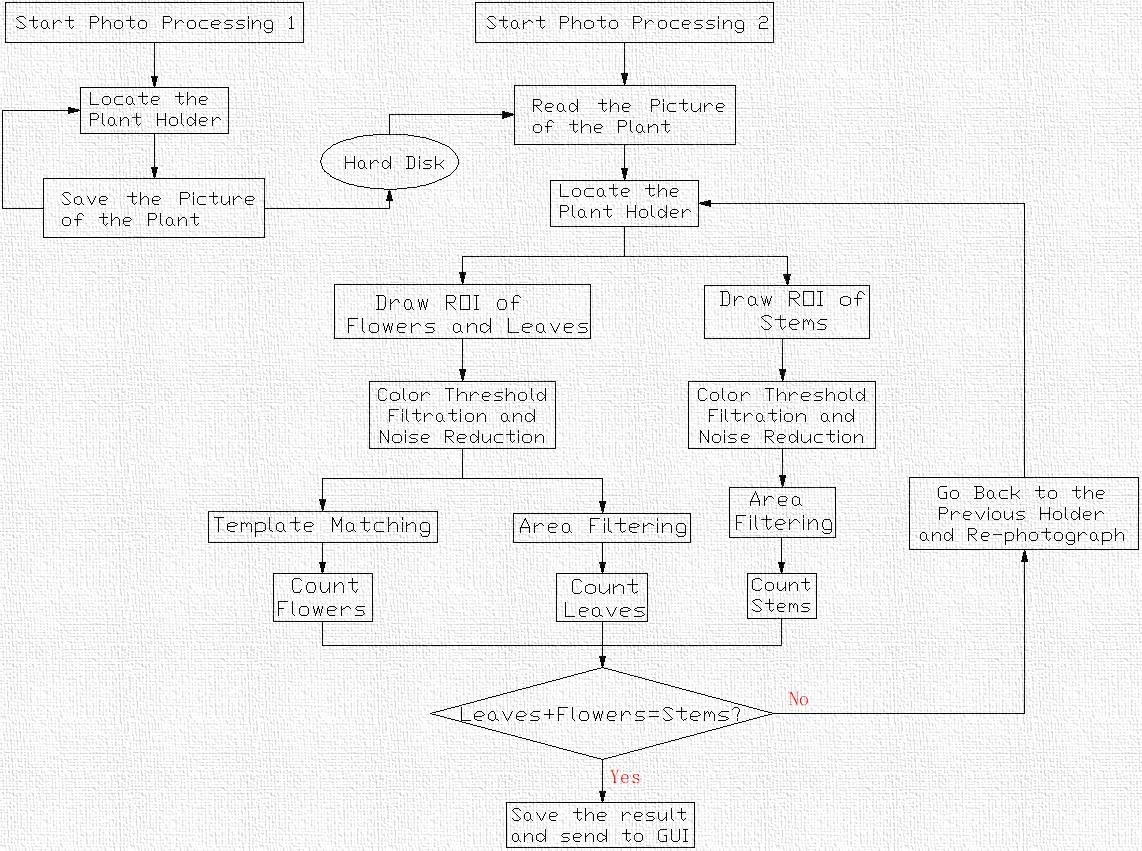
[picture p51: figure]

Figure 7-9 Logic flowchart of identification

## 8 Robot parameters

## 8.1 Weight of Robot

As shown in Figure 8-1, the robot is weighed using an electronic scale, and the weight of the

robot is M = 2.90 kg.

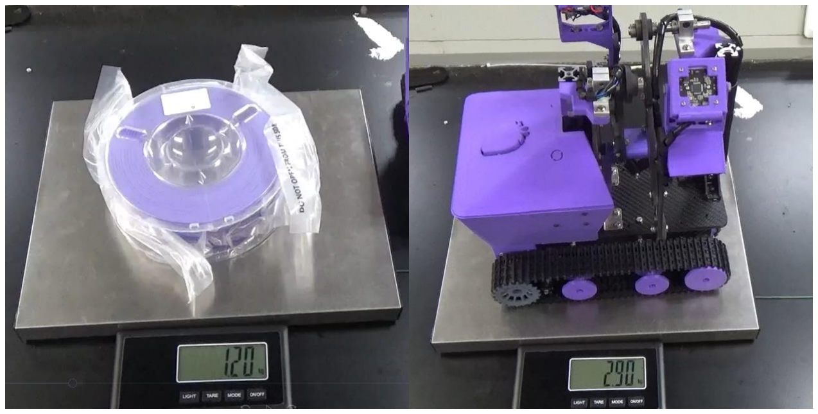
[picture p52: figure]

Figure 8-1 Robot weighing scene

## 8.2 The Contact Area of the Robot with the Ground

Since the length of the outer two long track tracks is l1=223.5 mm and the width is w1=45 mm,

and the length of the inner measured short tracks is l2=160mm and the width is w2=45 mm, the

contact area between the robot and the ground can be approximated as
S ≈ 2l1w1 + l2w2
= 2 × 223.5 × 45 + 160 × 45 = 27315 mm²
= 0.027 m²

## 8.3 The Pressure of the Robot on the Ground

From the data in 8.1 and 8.2 above, the pressure of the robot on the ground can be calculated as

P =

Mg
S
= 1040. 45 Pa

g - gravity acceleration, here take g = 9.8 kg/N

## 9 Parts List and Cost Analysis

As shown in Table 9-1, the total cost of our robot was $281.4. As shown in Table 9-2, the total

cost of computational devices to be integrated with our robot was $35.

Table 9-1 Total cost

Material | Unit Price (CNY) | Amount | Total price (CNY)
Carbon fiber | 450 | 1 | 450
Circuit board | 8 | 1 | 8
Raspberry Pi 4B | 226.59 | 1 | 226.59
Stepper motor | 30 | 2 | 60
Motor drive | 12 | 2 | 24
MG996 servo | 280 | 1 | 280
Camera | 75 | 2 | 150
Infrared sensor | 2.5 | 2 | 5
Aluminum profiles | 14 | 2 | 28
3D printing consumables | / | / | 85
Crawler | 6 | 3 | 18
Screws of different size(M3&M4) | / | 134 | 2
Nuts of different size(M3&M4) | / | 89 | 2
Lock nuts of M4 | / | 26 | 1.5
Slider | 20 | 2 | 40
Rail | 6 | 1 | 6
Angle iron | 0.3 | 9 | 2.7
Bearing | 3 | 10 | 30
Bearing support | 3 | 2 | 6
Bracket for servo | 2 | 1 | 2
Positioning pins | 2.5 | 2 | 5
Active wheel | 2 | 2 | 4
Switch and wires | / | / | 10
Sum | | | 1445.79 ($224)

Table 9-2 Computational devices

Material | Unit Price (CNY) | Amount | Total price (CNY)
Raspberry Pi 4B | 226.59 | 1 | 226.59 ($35)

As shown in Table 9-2, the only computational device we used was the Raspberry Pi 4B, which

cost $35, far less than the $100 limit set by the organizers.

## 10 Achievement of Objectives and Reflection

## 10.1 Achievement of Objectives

As shown in Table 10-1, based on our design, our robot is able to perform all the tasks perfectly.

Table 10-1 Achievement of Objectives

Objective | Amount | Score | Subtotal
Correct identification and mapping white flowers | 16 | 3 | 48
Correct identification and mapping yellow leaves | 11 | 1 | 11
Mapping the entire plant correctly | 12 | 3 | 36
Mapping the entire row correctly | 1 | 5 | 5
Have a navigation function without guidelines | / | / | √
Plants get damaged | 0 | 0 | 0
Transmits detection and counting results from the robot to a dedicated server computer. | / | / | √
Not any human intervention occurs | / | / | 10(bonus)
Have a start button that judges can use to initiate a competition trial and an emergency stop button to fully shut down the entire system. | / | / | √
Total | 110
Completion time | 00:25

## 10.2 Reflection

There is no denying that our design still has a lot of immaturity, and we are constantly reflecting

on our design and doing some thinking.

### 10.2.1 Rotation Speed

As shown in Figure 10-1, the camera extension mechanism unfolds through a ninety-degree

right angle, where a great torque is required from the servo and a certain initial speed is needed to

turn smoothly to the desired angle.

By adjusting the duty cycle of PWM wave to achieve flexible control of the servo, instead of

the original discrete angle rotation. Furthermore, we can add electronic components such as pressure sensors to get the current force of the mechanical structure and adjust the rotation speed of the servo

in real time, so as to extend the service life of each component.

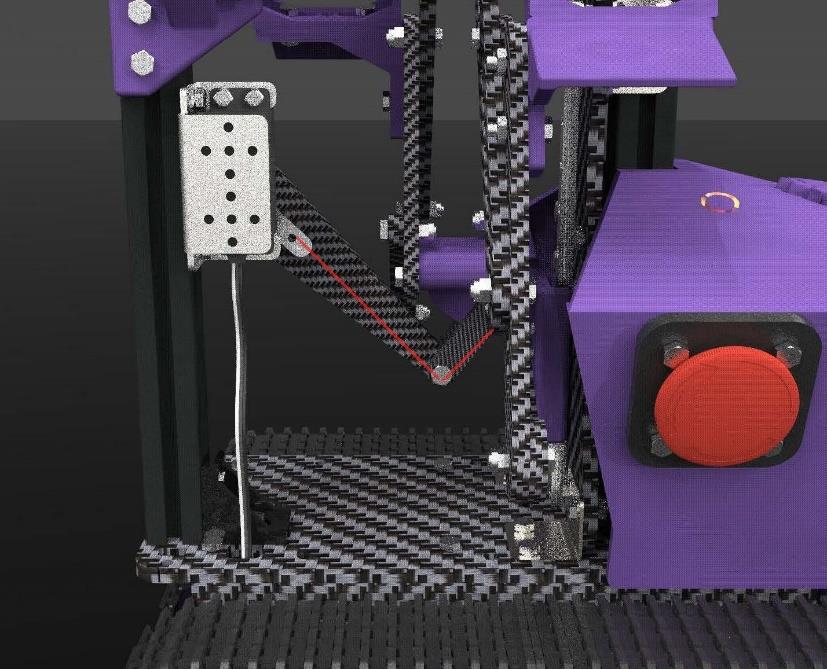
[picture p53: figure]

Figure 10-1 The right angle passed during the rotation

### 10.2.2 Exposed Components

Some of the electronic components of the robot are exposed on the outside and cannot cope

with weather conditions such as rain. Although strawberries are generally grown in agricultural

greenhouses, it is still necessary to take into consideration humidity and the influence of other

factors.

Using 3D printed parts to cover the electronic devices reasonably can prevent the circuit from

moisture performance changes, but also effectively prevent the metal from rusting and prolong the

service life. By designing the hollow structure, the wires can be placed inside the mechanical

structure.

### 10.2.3 Rods Connection

Due to size restrictions and other reasons, rod is screw-connected, yet to be optimized.

We hope to add bearings at the connection to reduce friction and protect the parts, and a servo

with less torque can be selected to save energy and cost.

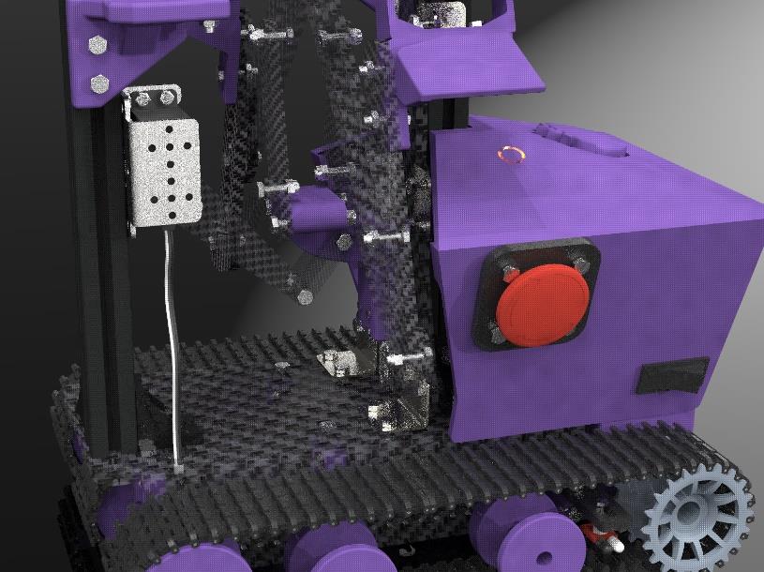
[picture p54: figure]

Figure 10-2 Rods and screws(perspective view)

### 10.2.4 Manual Adjustment of Camera

Although the camera connector of our device is equipped with the function of view adjustment,

the actual application is yet in need of a more intelligent and automatic adjustment method.

Small servos can be added to the camera connector to help adjust the field of view automatically.

### 10.2.5 Multi-Linkage Connection

Although we control the gap of rod-rod connection and rod- pedestal connection to be as small

as possible, the multi-stage connecting rods are still prone to slight vibrating after unfolded.

Add support mechanism to limit the horizontal displacement of the multi-rod after unfolded.

## 10.3 Versatile Applications

### 10.3.1 Multi-Rod Structure

On the one hand, the linkage connection and dimensions can be modified to meet the extension

requirements in different situations. On the other hand, end-effectors can be added to the linkage

mechanism to accomplish more demanding tasks.

### 10.3.2 Bilateral Process and Compatibility

On the one hand, the size and connection of the linkage can be adjusted so that the camera is

direct-above the plant after unfolding, so that the robot can achieve simultaneous recognition of

plants with different planting spacing. On the other hand, the algorithm of machine vision can be adjusted to recognize strawberry plants obliquely downward by adjusting on the existing mechanical

structure.

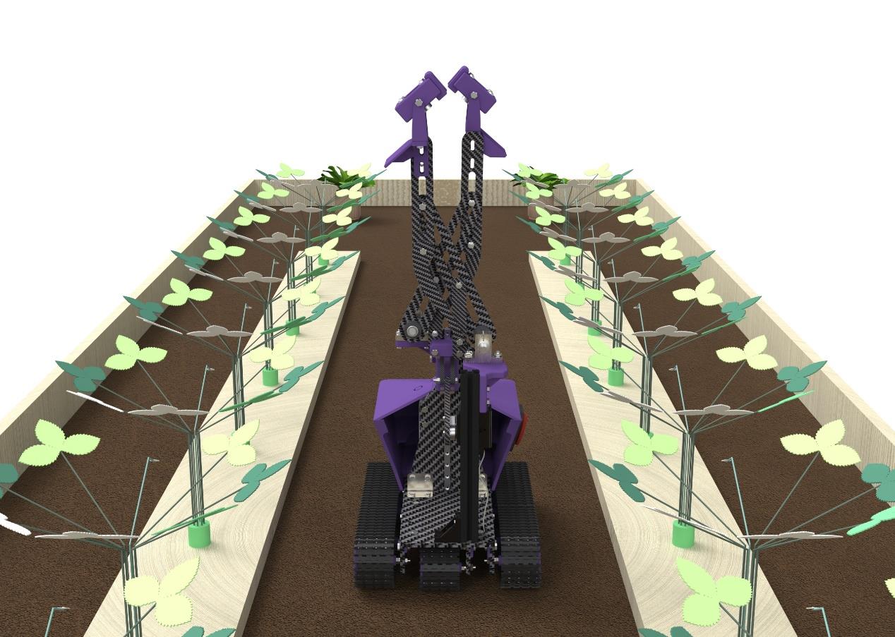
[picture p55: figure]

Figure 10-3 Schematic diagram of the robot for bilateral identification

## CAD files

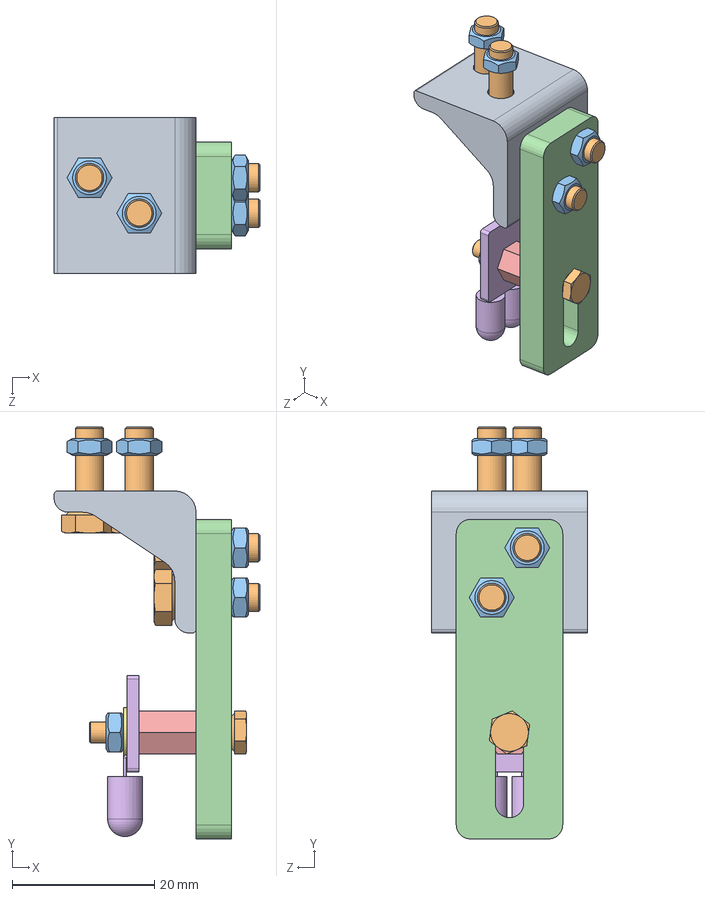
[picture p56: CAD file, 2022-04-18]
Model/红外连接件装配体.SLDASM
29.0 x 58.0 x 22.0 mm
红外连接件
hexagon head bolts-full thread gb x 5
hex nuts, style 1-grades ab gb x 5
红外_01_02
塑料螺柱
红外
plain washers--product grade c gb

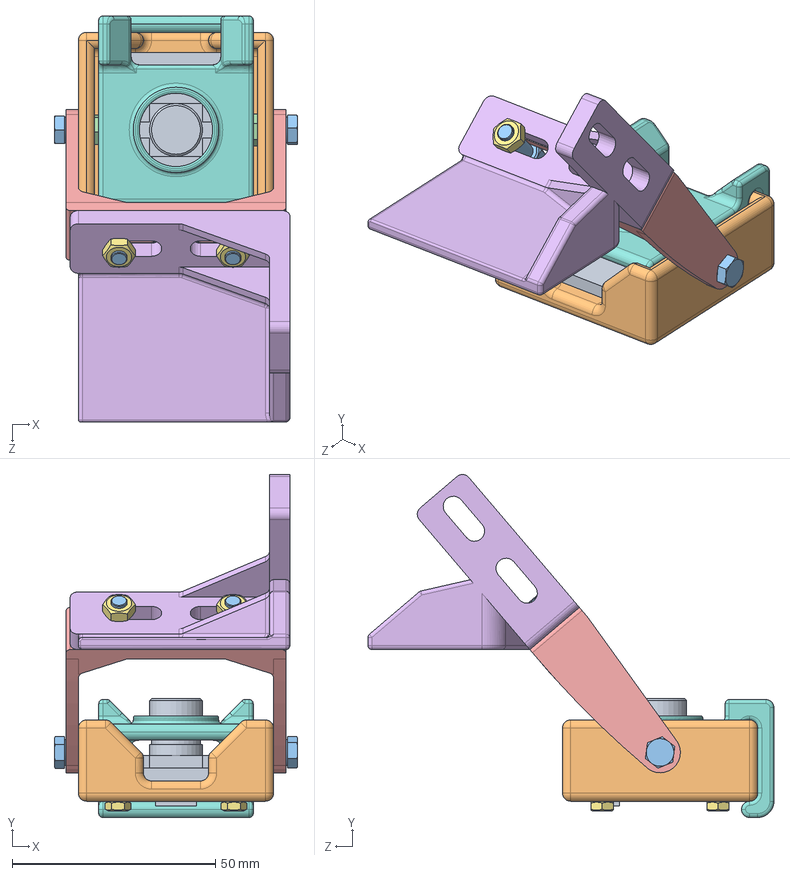
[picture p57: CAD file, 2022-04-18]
Model/摄像头案例_04.SLDASM
59.8 x 84.3 x 99.8 mm
摄像头_02
摄像头背板
hexagon head bolts-full thread gb x 8
锁紧螺丝 x 2
摄像头架_02
摄像头连接件_02_01
hex nuts, style 1-grades ab gb x 6
灯带连接件

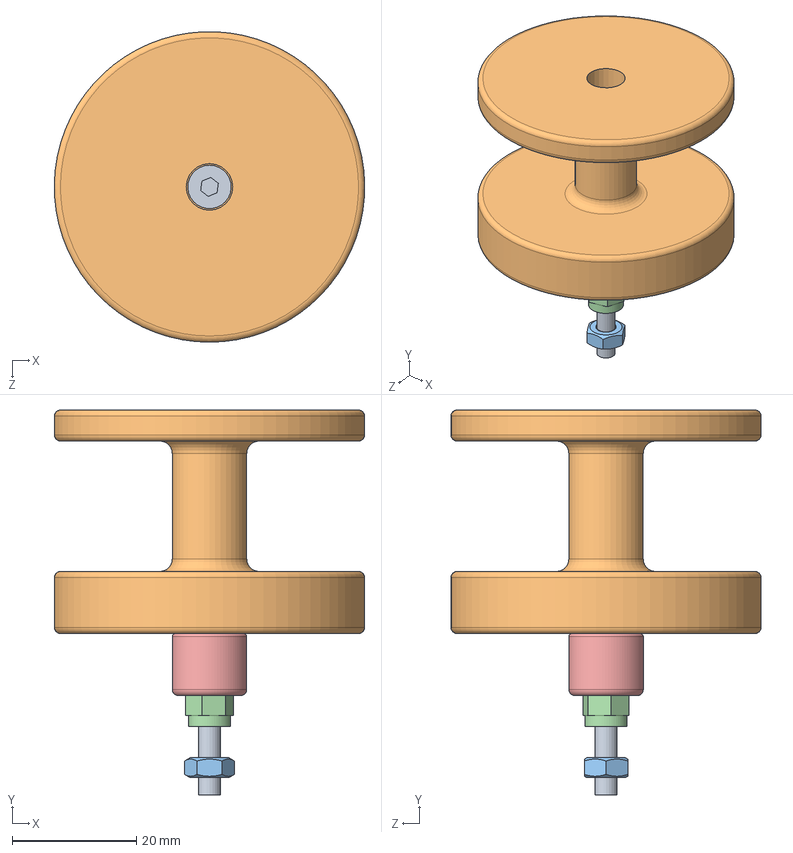
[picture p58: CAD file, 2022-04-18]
Model/承重轮装配体.SLDASM
50.0 x 62.0 x 50.0 mm
半牙螺丝M4 45
承重轮
hex nuts, style 1-grades ab gb
锁紧螺丝
承重轮_01_01

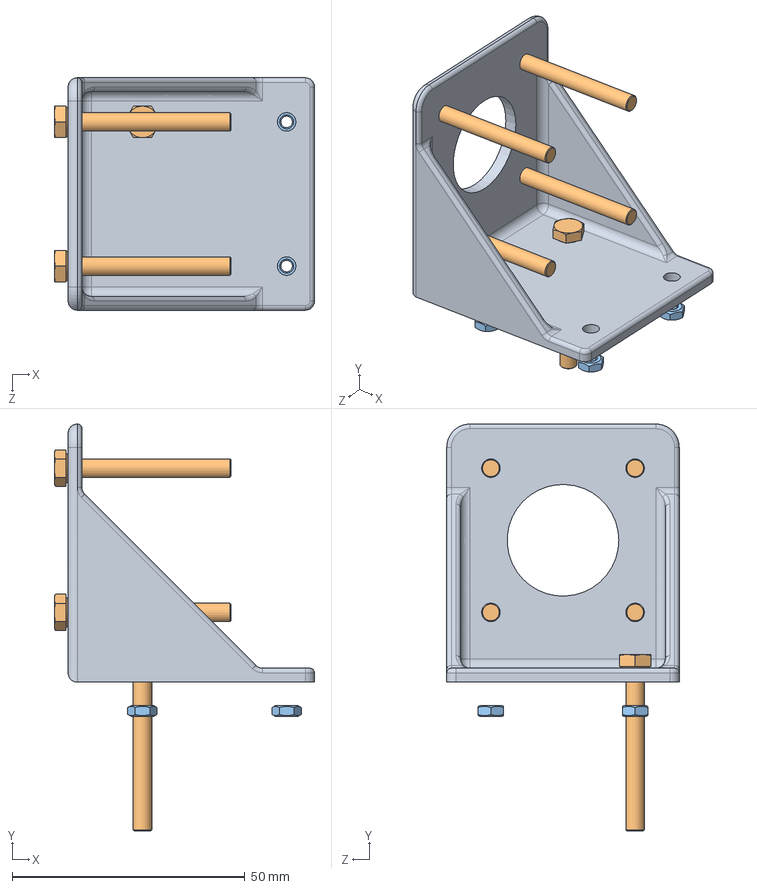
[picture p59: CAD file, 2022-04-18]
Model/电机架装配体.SLDASM
55.9 x 87.5 x 50.0 mm
电机架_2
hexagon head bolts-full thread gb x 5
hex nuts, style 1-grades ab gb x 4

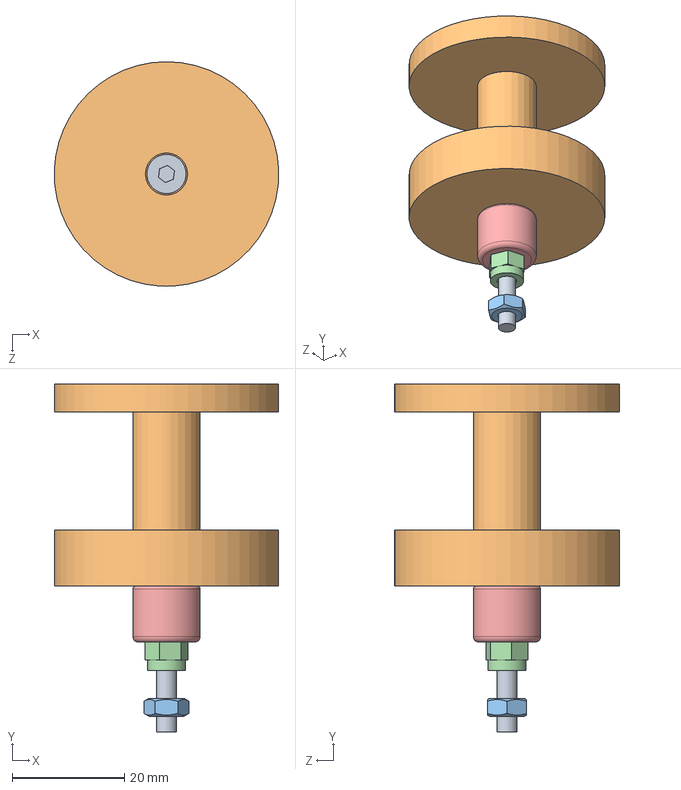
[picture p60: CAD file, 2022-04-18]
Model/承重轮装配体_小型.SLDASM
40.0 x 62.0 x 40.0 mm
半牙螺丝M4 45
承重轮_小型
hex nuts, style 1-grades ab gb
锁紧螺丝
承重轮_01_01

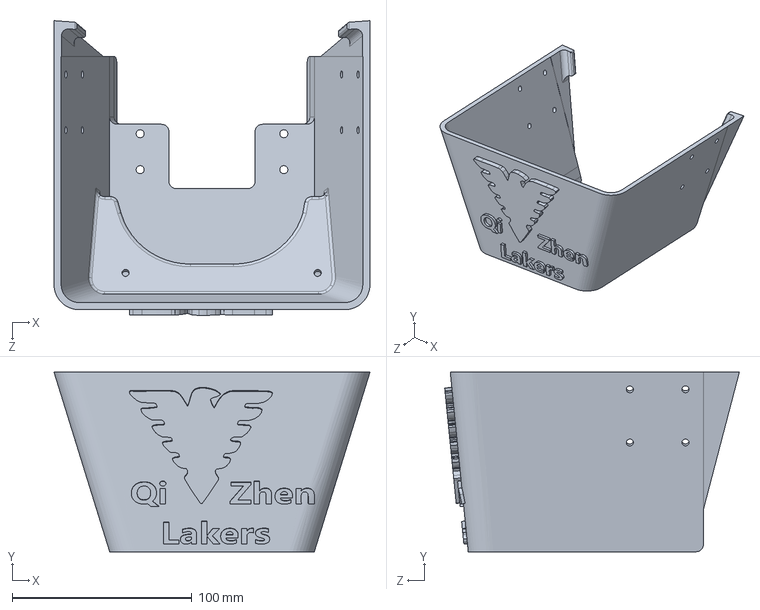
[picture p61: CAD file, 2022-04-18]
Model/收纳盒_03.SLDPRT
176.0 x 100.0 x 164.1 mm

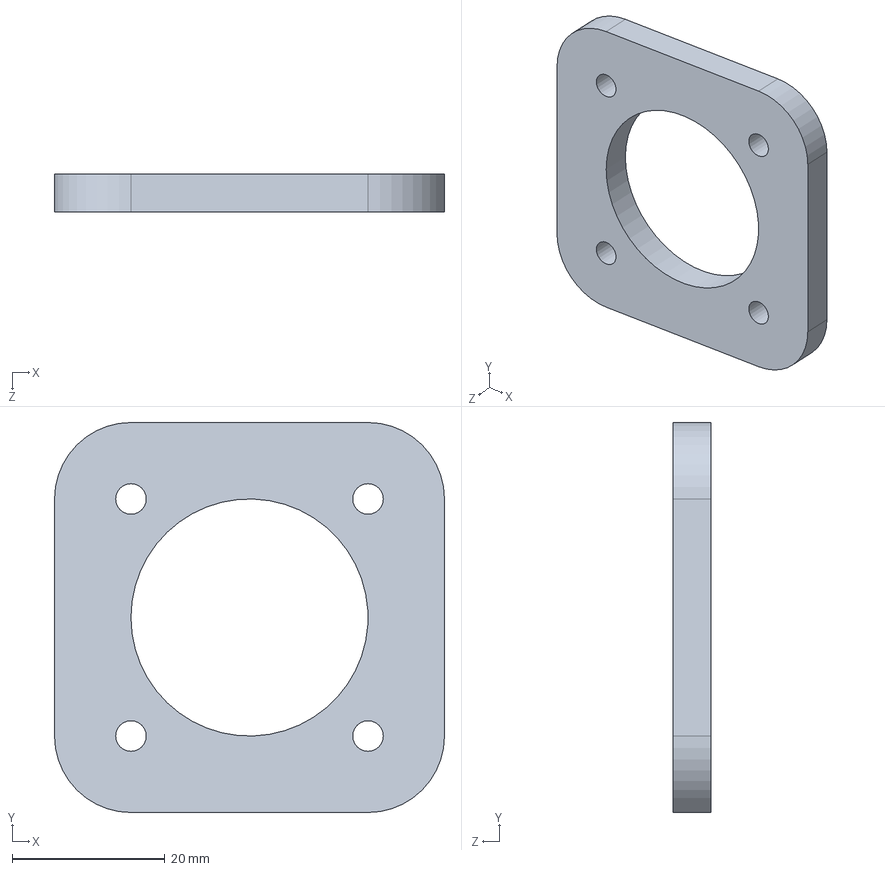
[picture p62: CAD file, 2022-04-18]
Model/开关外板.SLDPRT
51.0 x 51.0 x 5.00 mm

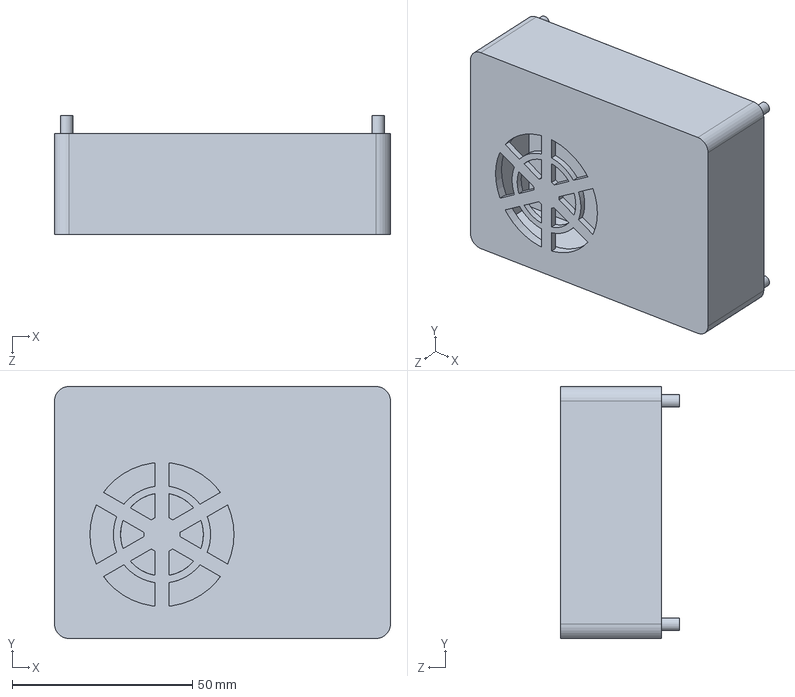
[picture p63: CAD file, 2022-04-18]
Model/RaspberryPi Model.SLDPRT
93.3 x 70.0 x 33.0 mm

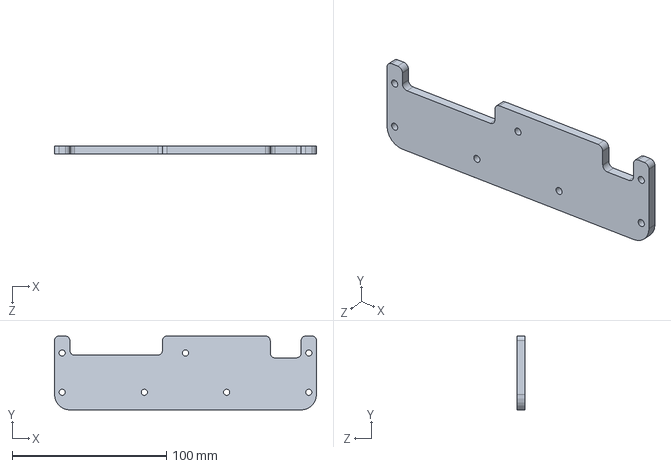
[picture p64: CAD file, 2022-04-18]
Model/侧板2.SLDPRT
170.0 x 48.0 x 5.00 mm

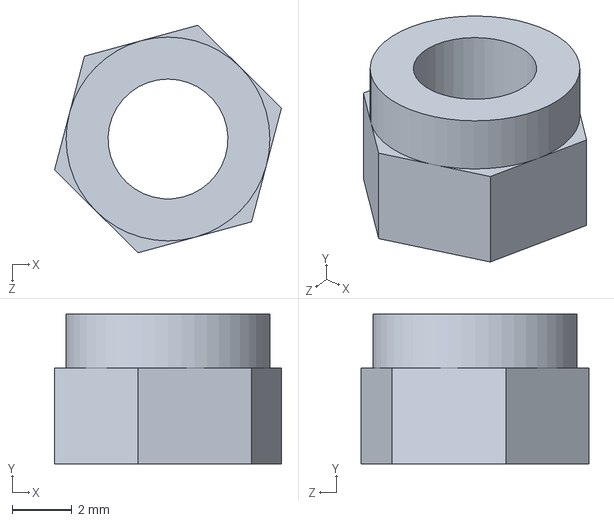
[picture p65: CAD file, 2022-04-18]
Model/锁紧螺丝.SLDPRT
7.58 x 5.00 x 7.59 mm

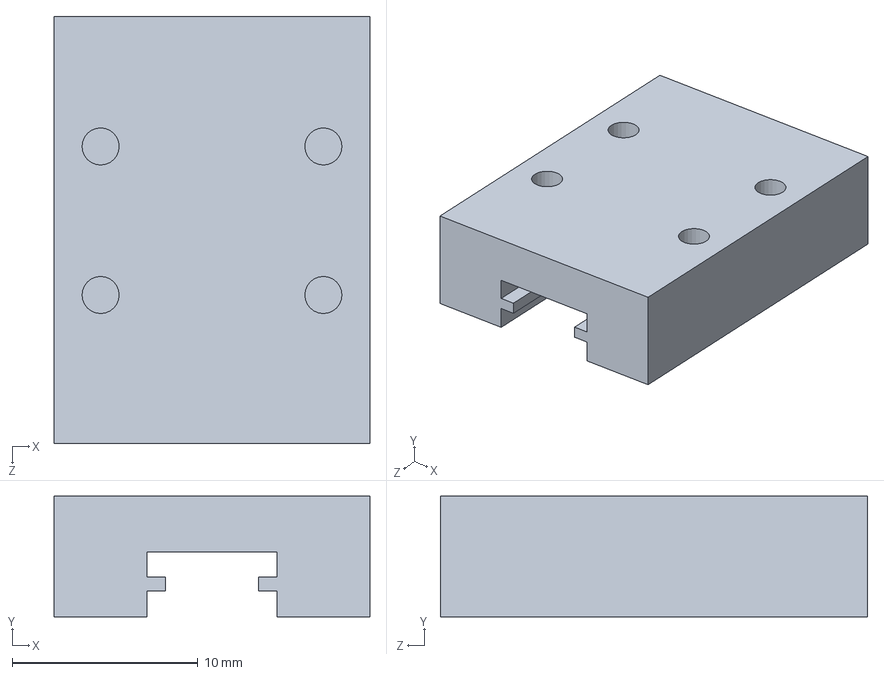
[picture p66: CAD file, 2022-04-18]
Model/滑块.SLDPRT
17.0 x 6.50 x 23.0 mm

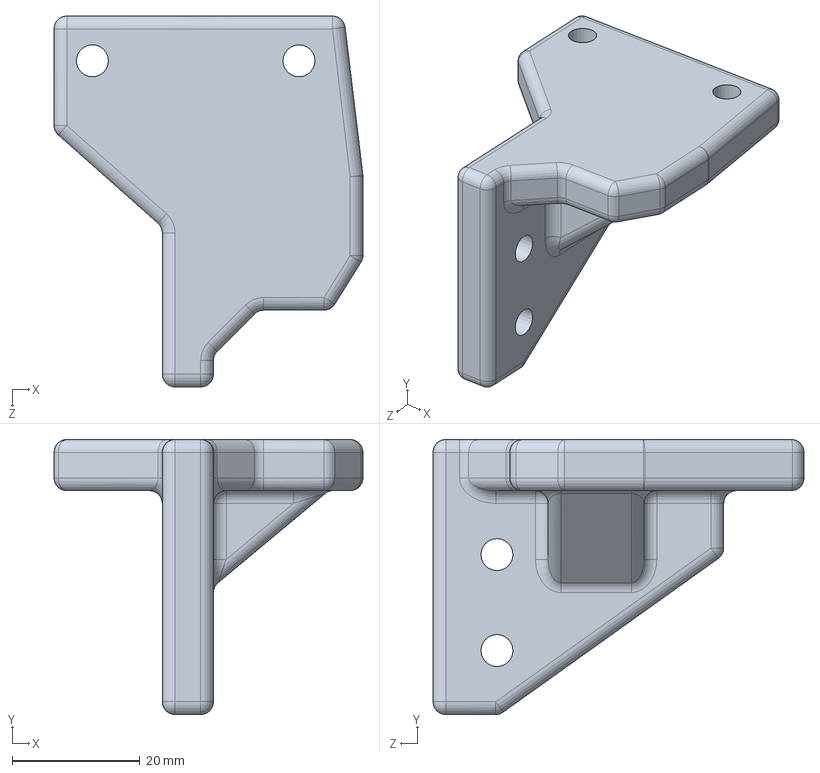
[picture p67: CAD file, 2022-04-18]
Model/轴承座连接件_06.SLDPRT
48.3 x 43.0 x 58.0 mm

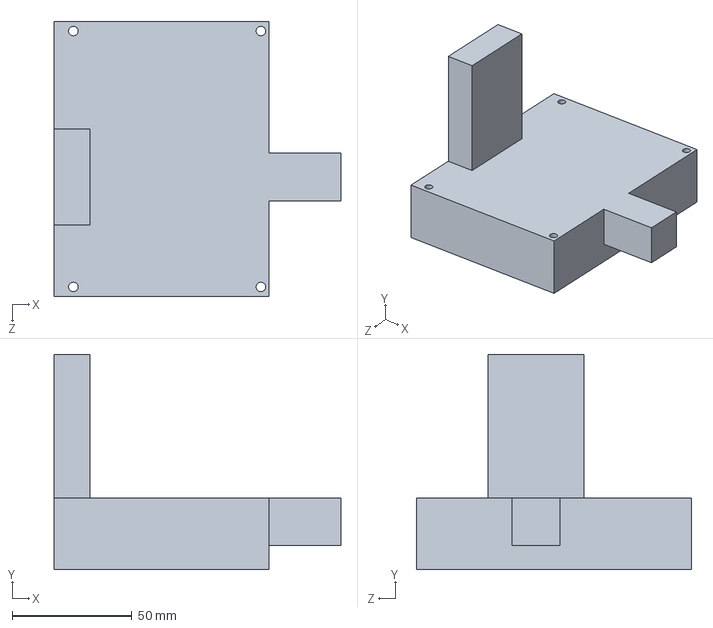
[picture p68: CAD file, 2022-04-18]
Model/简易电路板模型.SLDPRT
120.0 x 90.0 x 115.0 mm

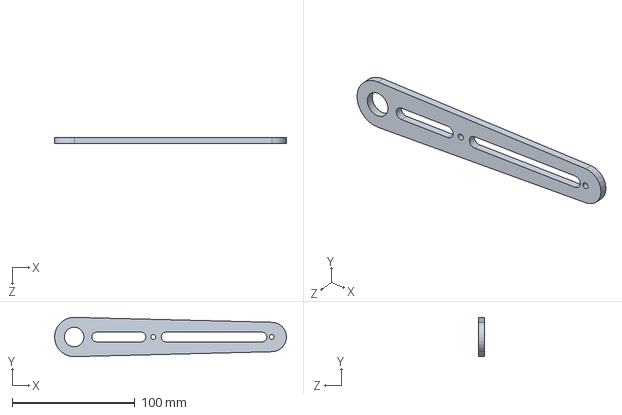
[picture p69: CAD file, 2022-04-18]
Model/末端杆_64.4+160_折叠_2.SLDPRT
189.0 x 32.0 x 5.00 mm

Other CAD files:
Model/履带链节单元.SLDPRT
Model/滑块连接件_4.SLDPRT
Model/升降连杆_40.SLDPRT
Model/滑轨.SLDPRT
Model/42x40步进电机.SLDPRT
Model/deep groove ball bearings gb.sldprt
Model/hex nuts, style 1-grades ab gb.sldprt
Model/hexagon head bolts gb.sldprt
Model/hexagon head bolts-full thread gb.sldprt
Model/misumi30X30型材.SLDPRT
Model/misumi30X30型材_2.SLDPRT
Model/plain washers--product grade c gb.sldprt
Model/主动轮_01.SLDPRT
Model/侧板1_2.SLDPRT
Model/侧板3_2.SLDPRT
Model/升降连杆_70_02.SLDPRT
Model/半牙螺丝M4 45.SLDPRT
Model/塑料螺柱.SLDPRT
Model/定位板_149.27_连接.SLDPRT
Model/底板连接件2.SLDPRT
Model/底板连接件3.SLDPRT
Model/底盘.SLDPRT
Model/开关.SLDPRT
Model/开关_红色.SLDPRT
Model/承重轮.SLDPRT
Model/承重轮_01_01.SLDPRT
Model/承重轮_小型.SLDPRT
Model/折叠杆_01_02.SLDPRT
Model/折叠杆_02_02.SLDPRT
Model/摄像头_02.SLDPRT
Model/摄像头架_02.SLDPRT
Model/摄像头背板.SLDPRT
Model/摄像头连接件_02_01.SLDPRT
Model/止推环.SLDPRT
Model/滑轨连接件_02.SLDPRT
Model/灯带连接件.SLDPRT
Model/电机架_2.SLDPRT
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

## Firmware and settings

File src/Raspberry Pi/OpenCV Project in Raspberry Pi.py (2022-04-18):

import cv2
import numpy as np
import sys
import RPi.GPIO as GPIO
import socket

client = socket.socket()  # anounce the kind of socket，and generate the connection object at the same time
client.connect(('192.168.123.26', 50007))  # start connection   ip:local ip    port:6961

# open a camera with certain index
frameWidth = 1280
frameHeight = 720
cap = cv2.VideoCapture(0)
cap.set(3, frameWidth)  # width
cap.set(4, frameHeight)  # height
# cap.set(10, 150)
# whether the camera is successfully opened
if cap.isOpened():
    print("camera ready.")
else:
    print("camera open failed. close.")
    # stop prg.
    sys.exit()

Type = ["WHITE", "YELLOW", "GREEN", "STEM"]
Color = [(255, 255, 255), (51, 255, 255), (0, 204, 0), (0, 204, 0)]
h_min = [68, 39, 68, 40]
h_max = [91, 71, 96, 98]
s_min = [0, 18, 50, 13]
s_max = [21, 82, 255, 69]
v_min = [255, 217, 124, 0]
v_max = [255, 255, 255, 255]

maskleave = cv2.imread("/home/pi/Desktop/maskl0508.jpg")
maskleaveHSV = cv2.cvtColor(maskleave, cv2.COLOR_BGR2HSV)
maskstem = cv2.imread("/home/pi/Desktop/masks0509.jpg")
maskstemHSV = cv2.cvtColor(maskstem, cv2.COLOR_BGR2HSV)
masktarget = cv2.imread("/home/pi/Desktop/target.jpg")  # get the area of rectangle including the holder
masktargetHSV = cv2.cvtColor(masktarget, cv2.COLOR_BGR2HSV)
lowermask = np.array([0, 0, 100])
uppermask = np.array([0, 0, 255])
mask_leave = cv2.inRange(maskleaveHSV, lowermask, uppermask)
mask_stem = cv2.inRange(maskstemHSV, lowermask, uppermask)
mask_target = cv2.inRange(masktargetHSV, lowermask, uppermask)


# what if put all of the process into the definition?
def getLeaves(img, i):
    imgHSV = cv2.cvtColor(img, cv2.COLOR_BGR2HSV)
    img_leave = cv2.bitwise_and(imgHSV, imgHSV, mask=mask_leave)
    lower = np.array([h_min[i], s_min[i], v_min[i]])
    upper = np.array([h_max[i], s_max[i], v_max[i]])
    maskcolor = cv2.inRange(img_leave, lower, upper)
    kernel = np.ones((3, 3), np.uint8)
    maskerode = cv2.erode(maskcolor, kernel, iterations=2)
    maskdilate = cv2.dilate(maskerode, kernel, iterations=4)
    contours, hierarchy = cv2.findContours(maskdilate, cv2.RETR_EXTERNAL, cv2.CHAIN_APPROX_NONE)
    count = 0
    for cnt in contours:
        area = cv2.contourArea(cnt)
        # print(area)
        if area > 14000:
            # print(area)
            cv2.drawContours(imgContour, cnt, -1, (120, 100, 100), 3)
            peri = cv2.arcLength(cnt, True)
            # print(peri)
            approx = cv2.approxPolyDP(cnt, 0.02 * peri, True)
            # print(len(approx))
            objCor = len(approx)
            x, y, w, h = cv2.boundingRect(approx)
            if objCor > 5:
                if area > 28000:
                    count = count + 2
                else:
                    count = count + 1
                cv2.rectangle(imgContour, (x, y), (x + w, y + h), Color[i], 2)
                cv2.putText(imgContour, Type[i],
                            (x + (w // 2) - 10, y + (h // 2) - 10), cv2.FONT_HERSHEY_COMPLEX, 0.7, Color[i],
                            2)
    # cv2.putText(imgContour, number, (500, 50), cv2.FONT_HERSHEY_COMPLEX, 0.7, (0, 0, 255), 2)
    # print("end")
    return count


def getStems(img, i):
    contours, hierarchy = cv2.findContours(image, cv2.RETR_EXTERNAL, cv2.CHAIN_APPROX_NONE)
    count = 0
    for cnt in contours:
        area = cv2.contourArea(cnt)
        # print(area)
        if area > 900:
            # print(area)
            cv2.drawContours(imgContour, cnt, -1, (120, 100, 100), 3)
            peri = cv2.arcLength(cnt, True)
            # print(peri)
            approx = cv2.approxPolyDP(cnt, 0.02 * peri, True)
            # print(len(approx))
            objCor = len(approx)
            # print(objCor)
            x, y, w, h = cv2.boundingRect(approx)
            # if objCor > 5:
            count = count + 1
            cv2.rectangle(imgContour, (x, y), (x + w, y + h), Color[i], 2)
    return count


def StopTarget(image):
    imgHSVtarget = cv2.bitwise_and(image, image, mask=mask_target)
    lower = np.array([40, 30, 135])
    upper = np.array([90, 210, 255])
    mask = cv2.inRange(imgHSVtarget, lower, upper)  # get the threshold of green leaves
    kernel = np.ones((3, 3), np.uint8)
    mask = cv2.dilate(mask, kernel, iterations=2)  # dilate
    contours, hierarchy = cv2.findContours(mask, cv2.RETR_EXTERNAL, cv2.CHAIN_APPROX_NONE)
    for cnt in contours:
        area = cv2.contourArea(cnt)
        print(area)
        if area > 2000:
            # peri = cv2.arcLength(cnt, True)
            # print(peri)
            # approx = cv2.approxPolyDP(cnt, 0.02 * peri, True)
            # print(len(approx))
            return True
    else:
        return False


def StopStems(image, i):
    lower = np.array([h_min[i], s_min[i], v_min[i]])
    upper = np.array([h_max[i], s_max[i], v_max[i]])
    imgHSVstem = cv2.bitwise_and(image, image, mask=mask_stem)
    mask = cv2.inRange(imgHSVstem, lower, upper)
    kernel = np.ones((3, 3), np.uint8)
    maskerode = cv2.erode(mask, kernel, iterations=0)
    maskdilate = cv2.dilate(maskerode, kernel, iterations=2)
    contours, hierarchy = cv2.findContours(maskdilate, cv2.RETR_EXTERNAL, cv2.CHAIN_APPROX_NONE)
    count = 0
    for cnt in contours:
        area = cv2.contourArea(cnt)
        # print(area)
        if area > 900:
            # print(area)
            # cv2.drawContours(imgContour, cnt, -1, (120, 100, 100), 3)
            # peri = cv2.arcLength(cnt, True)
            # print(peri)
            # approx = cv2.approxPolyDP(cnt, 0.02 * peri, True)
            # print(len(approx))
            # objCor = len(approx)
            # print(objCor)
            # x, y, w, h = cv2.boundingRect(approx)
            # if objCor > 5:
            count = count + 1
            # cv2.rectangle(imgContour, (x, y), (x + w, y + h), Color[i], 2)
    if count >= 6:
        return True
    else:
        return False


message = ['0', '0', '0', '0', '0', '0', '0', '0', '0', '0', '0', '0', '0', '0', '0', '0', '0', '0', '0', '0', '0', '0',
           '0', '0']
x1 = -2
x2 = -1
complete = 0
while True:
    success, img = cap.read()
    imgContour = img.copy()
    GPIO.setmode(GPIO.BOARD)
    GPIO.setwarnings(False)
    GPIO.setup(33, GPIO.IN)
    GPIO.setup(35, GPIO.IN)
    GPIO.setup(37, GPIO.OUT)
    GPIO.output(37, 0)

    imgHSV = cv2.cvtColor(img, cv2.COLOR_BGR2HSV)

    if StopTarget(imgHSV) and StopStems(imgHSV, 3):
        GPIO.output(37, 1)  # stop
        sum_allleaves = sum_stems = sum_whiteleaves = 0
        x1 += 2
        x2 += 2
        index = 0
        while index < 5:
            success, img = cap.read()
            imgContour = img.copy()
            imgHSV = cv2.cvtColor(img, cv2.COLOR_BGR2HSV)
            img_leave = cv2.bitwise_and(imgHSV, imgHSV, mask=mask_leave)
            img_stem = cv2.bitwise_and(imgHSV, imgHSV, mask=mask_stem)

            # get all the leaves
            count_allleaves = 0
            for i in range(0, 3):
                lower = np.array([h_min[i], s_min[i], v_min[i]])
                upper = np.array([h_max[i], s_max[i], v_max[i]])
                mask = cv2.inRange(img_leave, lower, upper)
                kernel = np.ones((3, 3), np.uint8)
                newmask1 = cv2.erode(mask, kernel, iterations=2)
                newmask2 = cv2.dilate(newmask1, kernel, iterations=4)
                count_leaves = getLeaves(newmask2)
                count_allleaves += count_leaves

            # get white leaves
            i = 0
            lower = np.array([h_min[i], s_min[i], v_min[i]])
            upper = np.array([h_max[i], s_max[i], v_max[i]])
            mask = cv2.inRange(img_leave, lower, upper)
            kernel = np.ones((3, 3), np.uint8)
            newmask3 = cv2.erode(mask, kernel, iterations=2)
            newmask4 = cv2.dilate(newmask3, kernel, iterations=4)
            count_whiteleaves = getLeaves(newmask4)

            # get stems
            i = 3
            lower = np.array([h_min[i], s_min[i], v_min[i]])
            upper = np.array([h_max[i], s_max[i], v_max[i]])
            mask = cv2.inRange(img_stem, lower, upper)
            kernel = np.ones((3, 3), np.uint8)
            newmask5 = cv2.erode(mask, kernel, iterations=0)
            newmask6 = cv2.dilate(newmask5, kernel, iterations=2)
            count_stems = getStems(newmask6)

            sum_allleaves += count_allleaves
            sum_whiteleaves += count_whiteleaves
            sum_stems += count_stems
            index += 1

        result_allleaves = round(sum_allleaves/index)
        result_whiteleaves = round(sum_whiteleaves/index)
        result_stems = round(sum_stems/index)
        # if result_stems < 6:
        #     result_stems = 6
        # elif result_stems > 8:
        #     result_stems = 8
        result_flowers = result_stems - result_allleaves
        # if result_whiteleaves >= 3:
        #     result_whiteleaves = 3
        #     result_flowers = 0
        # if result_flowers < 0:
        #     result_flowers = 0
        # elif result_flowers > 4:
        #     result_flowers = 4
        result_text = 'whitelaves: ' + str(result_whiteleaves) + 'flowers: ' + str(result_flowers)
        cv2.putText(imgContour, result_text, (50, 50), cv2.FONT_HERSHEY_COMPLEX, 0.7, (0, 0, 0), 2)

        message[x1] = str(result_whiteleaves)
        message[x2] = str(result_flowers)
        cv2.imwrite('/home/pi/' + 'image' + str(x1/2 + 1) + '.png', imgContour)
        msg = ''.join(message)
        print(msg)
        client.send(msg.encode("utf-8"))  # deliver the message to the server

        GPIO.output(37, 0)
        print("wait for next task")

    client.send(msg.encode("utf-8"))  # deliver the message to the server
    cv2.imshow("imgContour", imgContour)
    cv2.waitKey(1)

    if x1 == 22:
        cv2.waitKey(1500)
        data = client.recv(1024)  # accept the message
        print('client_recv:', data.decode())  # print the message
        break

    GPIO.cleanup()

client.close()  # Finally,remember to shut up the client
